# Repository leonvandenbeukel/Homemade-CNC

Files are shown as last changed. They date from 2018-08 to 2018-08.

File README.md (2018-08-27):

## Homemade CNC 

### Warning!

If you want to build one yourself you can download all the necessary files from the V2 directory but I don't have enough time to give you much support so build it at your own risk! :smiley:

### Introduction

This is the second version of my DIY homemade CNC. It's a complete redesign because of some issues that I had with the first one. The main issue with the first version was that the wooden Y axis was getting warped (by moisture I guess). Also the bearings were too small and the aluminium X rails were not strong enough to carry the weight. That's why I've switched over to use 20mm x 20mm square steel tubes for both Y- and X axis. 

### YouTube video

<a href="https://youtu.be/24RslguGy58" target="_blank">Click to view: Homemade CNC with 3D printed parts V2</a>

### Design

I've designed the 3D printed parts with Fusion 360 and used Inkscape for the Y axis drilling template. To control the machine I'm using an Arduino UNO with GRBL firmware and an Arduino CNC Shield. There are plenty of tutorials to find on how to connect and use it so I did not show it in the video. Here are some useful links:

* [GRBL](https://github.com/gnea/grbl)
* [Arduino CNC Shield](https://blog.protoneer.co.nz/arduino-cnc-shield/)

### 3D Printing

The 3D printer I use is an Anet A8. The parts are printed with PLA, mostly 20% infill and 0.2 or 0.4 setting. Use higher infill for parts that must be stronger, for example the stepper motor mounts.

### Cost estimation

* [Link to Google Sheet](https://docs.google.com/spreadsheets/d/e/2PACX-1vQY4hpT6myB3YeNzVlFZfTstJrkYJus8l174NMnyP0J1uP0NMzN-vVNtQ_hvMKP-WXqgEPKxjZSqRSU/pubhtml "Link to Google Sheet")

### Dimensions

Base front multiplex Y panels are 710 x 180 x 22 mm or 28" x 7" x 0.86".
The laminated MDF X Axis side panels are 180 x 370 mm or 7" x 14.4".

The tubes are 20mm x 20mm (0.78") square steel tubes. The length of the Y Axis tubes is 1000mm (40") and the length for the X Axis is approx. 820mm (32"). As an alternative you could also use other dimensions than 20mm x 20mm (maybe even rounded tubes) as long as they are approximately that size.
The Z axis tubes are 15mm x 15mm (0.59") aluminium square tubes, approx. 215mm long (8.5"). You should measure this for yourself, check the video build.

The threaded rods for Y and X rails are 8 mm (0.31") stainless steel.

### Power and motors

To power the NEMA 17 stepper motors I've converted an old ATX PC power supply and used the 12V output. The type of stepper motors I use for the Y- and Z axis are: 17HS19-2004S1, the type for the X axis is: 42BYGHW811. For the wiring I've used CAT5 network cable.

### Software that I mostly use to generate and send GCode:

* bCNC (https://github.com/vlachoudis/bCNC)
* Universal Gcode Sender (https://github.com/winder/Universal-G-Code-Sender)
* Easel by Inventables (http://easel.inventables.com)
* Fusion 360 with CAM (https://www.autodesk.com/products/fusion-360/students-teachers-educators)

### Help me make more stuff!

All my designs are free to use! If you want to support my work you can donate:



Thanks!

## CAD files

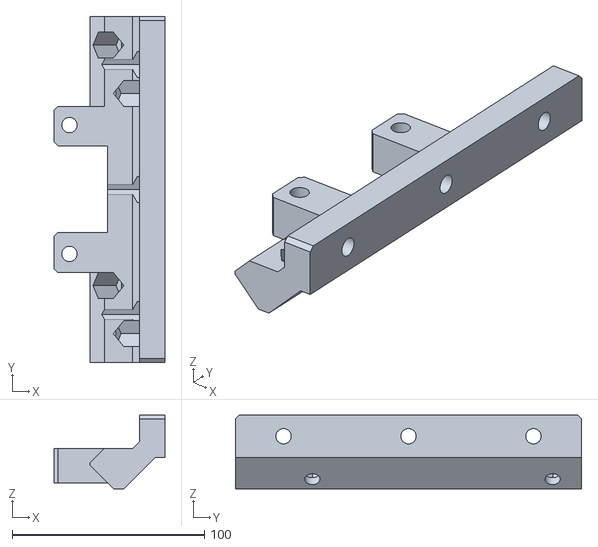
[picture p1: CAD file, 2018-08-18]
V2/Universal Y and X Slider Mount.stl
57.6 x 180.0 x 38.4

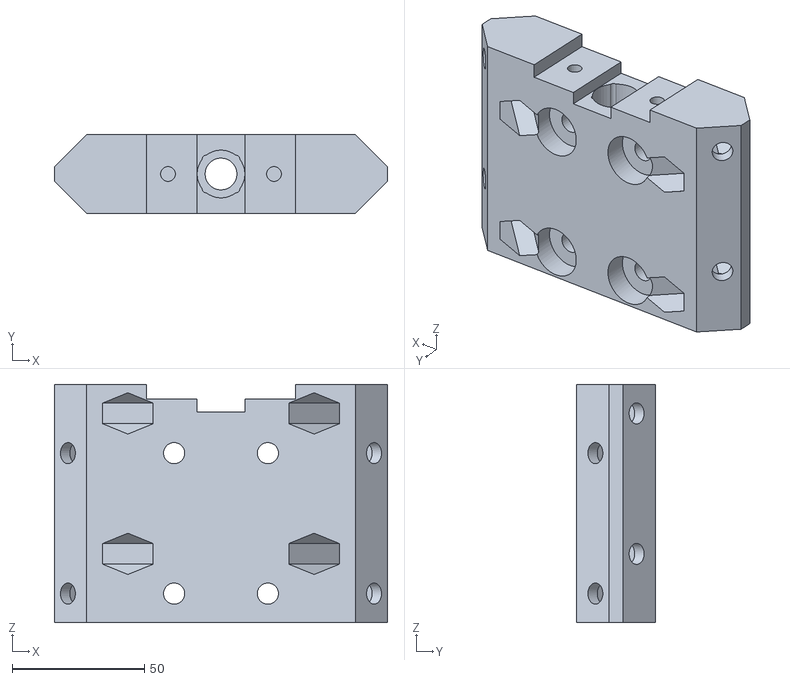
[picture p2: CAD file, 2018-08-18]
V2/Z Axis Mount.stl
125.7 x 29.7 x 90.0

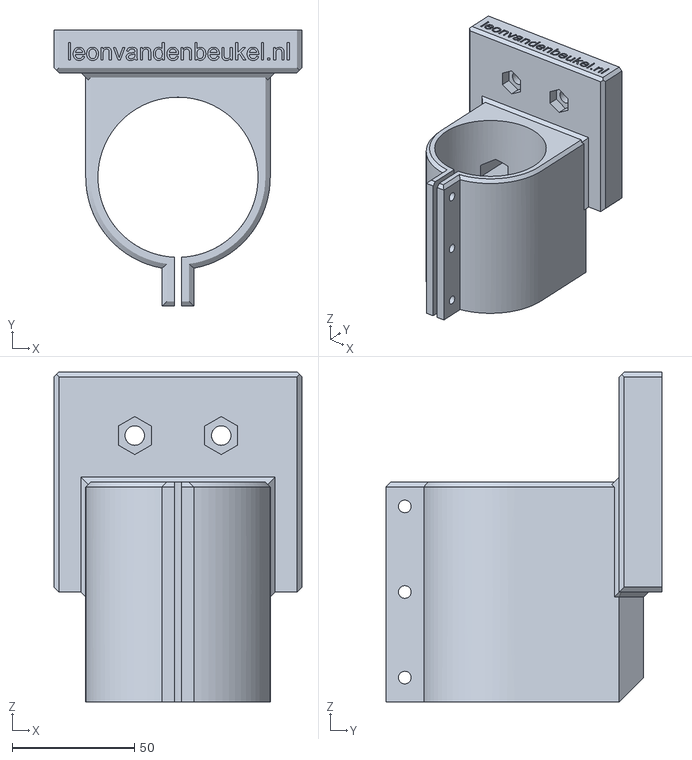
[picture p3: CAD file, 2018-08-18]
V2/Z Axis Router Mount.stl
101.4 x 113.1 x 135.0

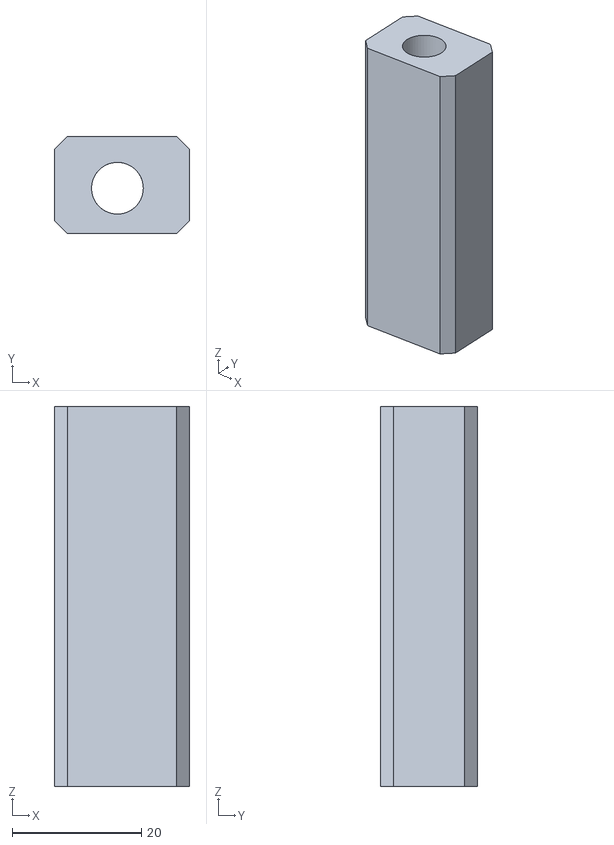
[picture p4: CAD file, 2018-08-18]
V2/X Axis Mount Spacer A.stl
20.9 x 15.0 x 58.7

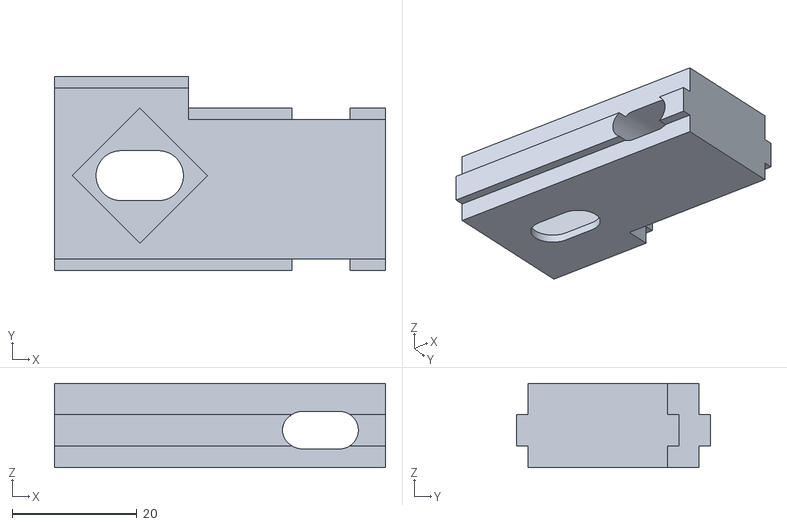
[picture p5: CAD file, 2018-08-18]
V2/Z Axis Slider Bottom.stl
53.0 x 31.0 x 13.5

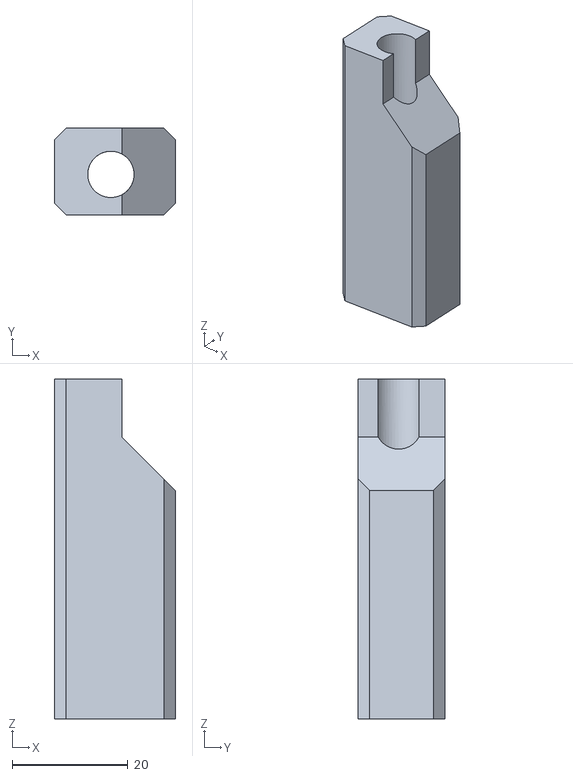
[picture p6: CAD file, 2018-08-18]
V2/X Axis Mount Spacer B.stl
20.9 x 15.0 x 58.7

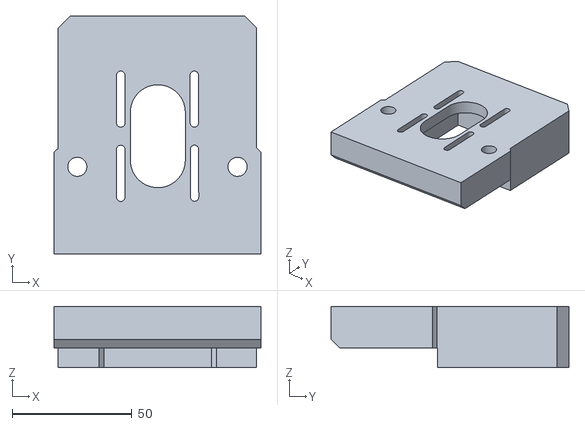
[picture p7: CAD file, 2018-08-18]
V2/Z Axis Stepper Motor Mount.stl
86.6 x 99.4 x 25.6

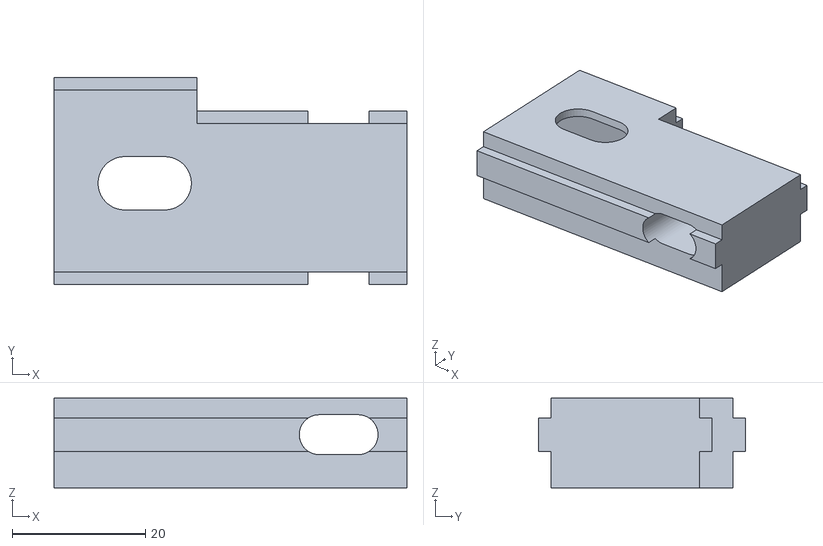
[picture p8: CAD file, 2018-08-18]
V2/Z Axis Slider Top.stl
53.0 x 31.0 x 13.5

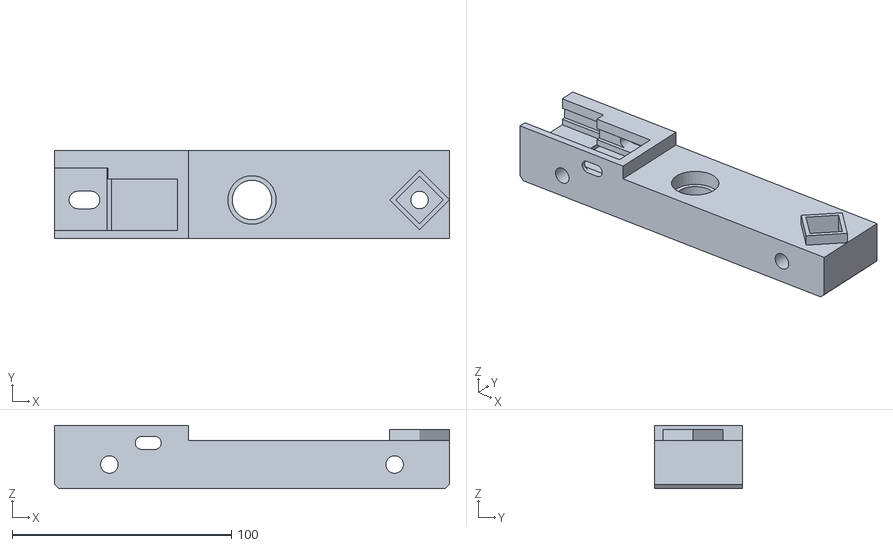
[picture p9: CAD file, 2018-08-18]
V2/Z Axis Bottom.stl
180.0 x 40.0 x 28.9

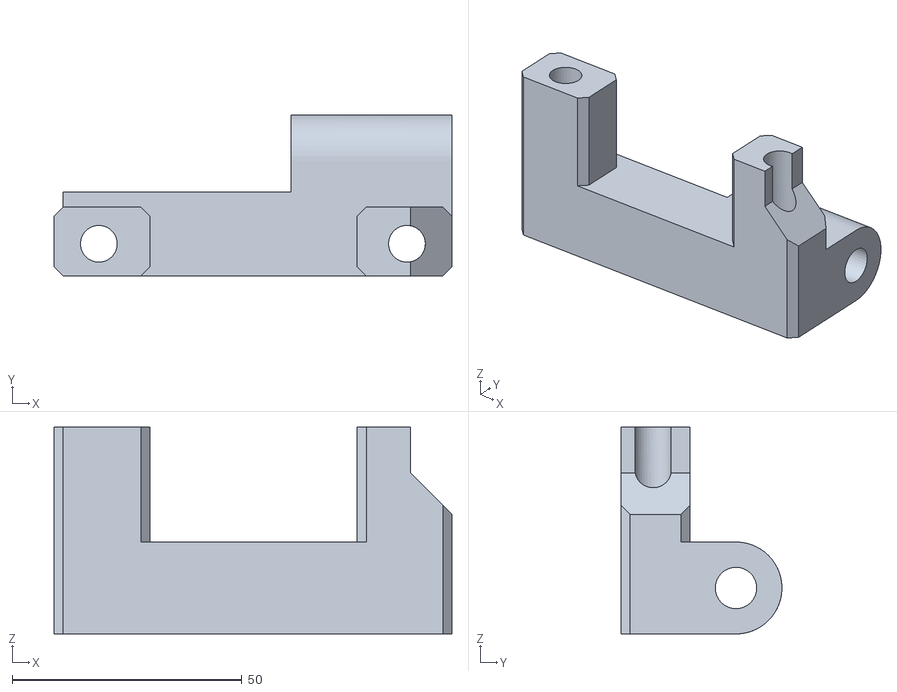
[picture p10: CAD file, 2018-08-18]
V2/X Axis Mount.stl
86.6 x 35.0 x 45.0

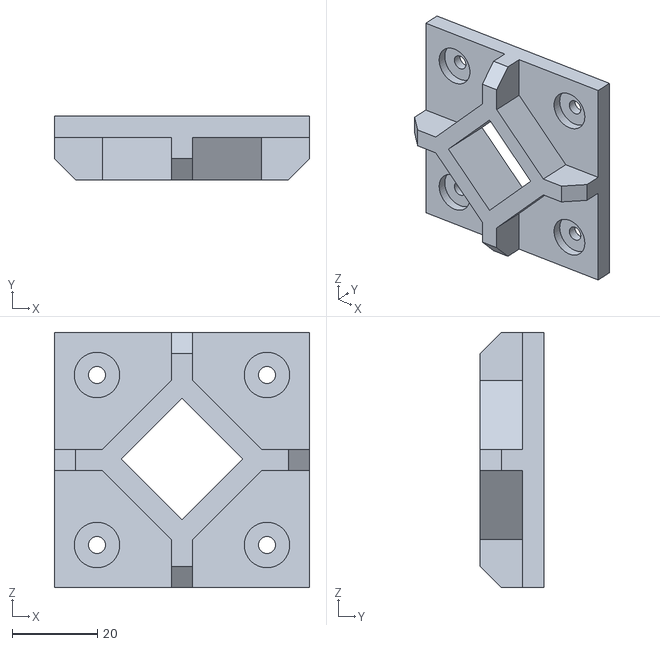
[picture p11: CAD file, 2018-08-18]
V2/Y Axis Rails Mount 20x20.stl
60.0 x 15.0 x 60.0

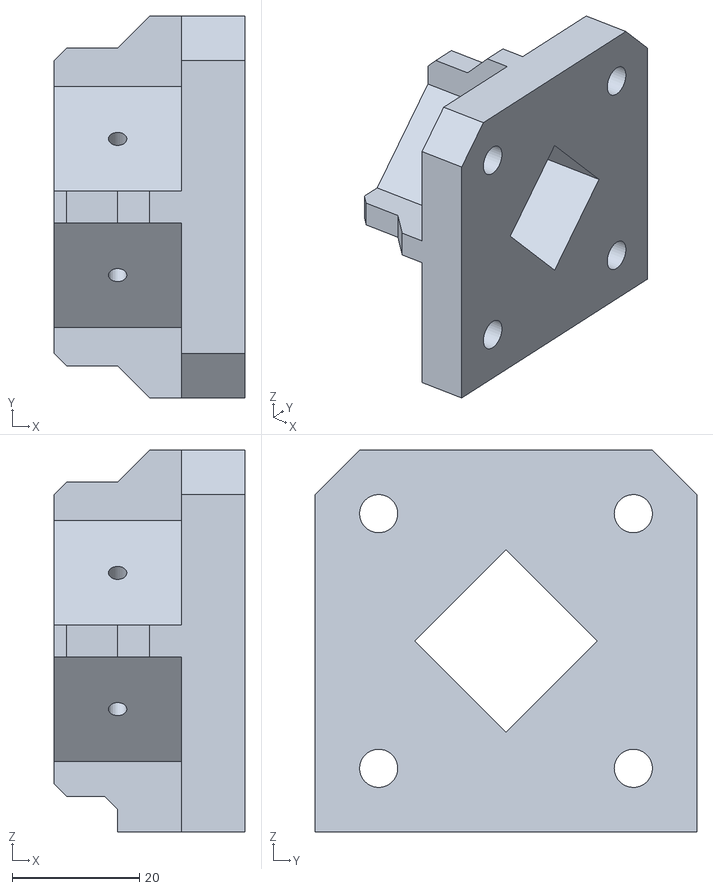
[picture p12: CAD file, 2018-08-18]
V2/X Axis Rails Mount Outside.stl
30.0 x 60.0 x 60.0

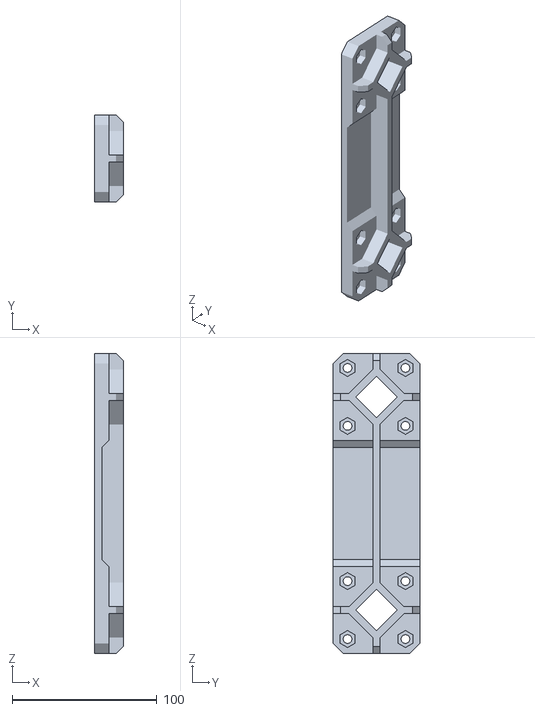
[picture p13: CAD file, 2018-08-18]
V2/X Axis Rails Mount Inside.stl
20.0 x 60.0 x 207.2

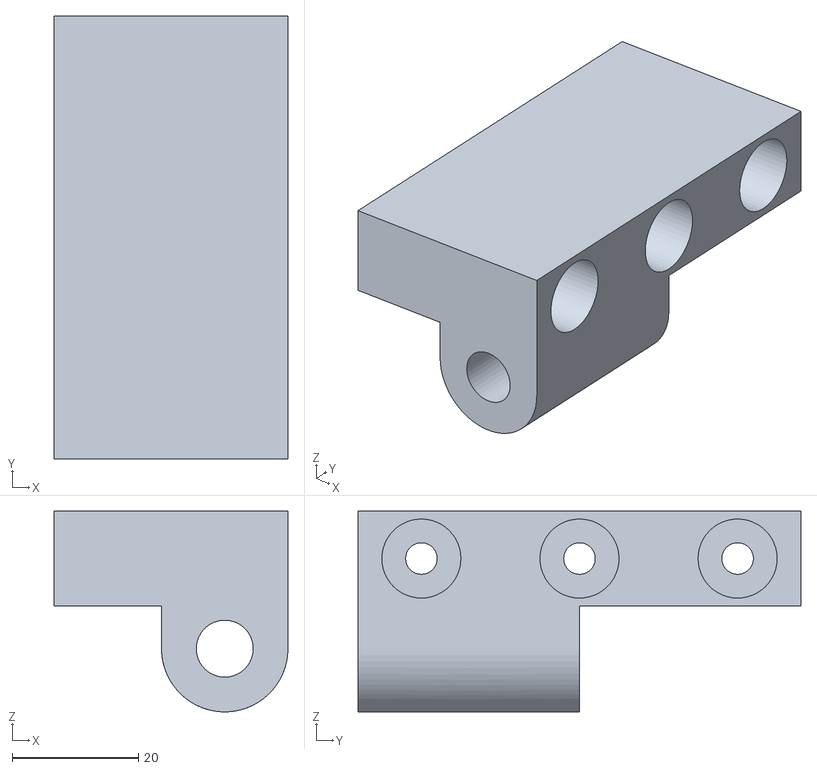
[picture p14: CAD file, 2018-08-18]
V2/Y Axis Threaded Rod Mount.stl
37.0 x 70.0 x 31.7

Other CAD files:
V2/Z Axis Top.stl
V2/Z Axis Mount Backlash.stl
V2/Stepper Motor Mount.stl
V2/Bearing Holder.stl
V1/Router Holder.stl
V1/X Rail holder.stl
V1/Y Carrier Support.stl
V1/Y Carrier.stl
V1/Y Rail Connect Plate.stl
V1/Z Bottom layer.stl
V1/Z First Mounting Plate.stl
V1/Z Forth layer.stl
V1/Z Second Mounting Plate.stl
V1/Z Second layer.stl
V1/Z Third layer.stl
V1/Z Top.stl

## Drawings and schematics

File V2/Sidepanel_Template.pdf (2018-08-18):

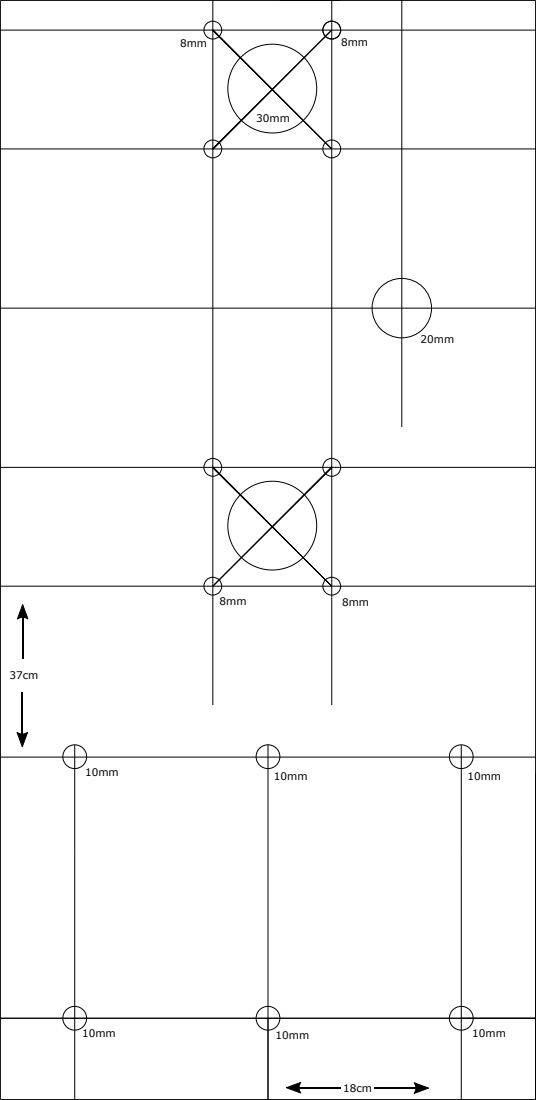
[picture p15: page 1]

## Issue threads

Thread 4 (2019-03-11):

Modifications for DW618

pnbr0014, 2019-03-11:
Hey man this is one amazing build! I would like to build this however, I have a DeWalt DW618 it's a 2 1/4 up router which I think is bigger than yours. If I were to modify the size of the spindle holder to accommodate my router would the rest if the parts be able to handle the extra weight?

pnbr0014, 2019-03-11:
Sorry for some reason it submitted twice

christianlupus, 2019-03-12:
> Sorry for some reason it submitted twice

Then you might close one of the opened issues.

pnbr0014, 2019-03-12:
K I closed it.

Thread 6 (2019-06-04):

Bill of Materials for how many of each STL file?

optimizedsms, 2019-06-04:
Do you happen to have a bill of materials for how many of each STL file needs to be printed?
Thank you.

rjones96, 2019-08-17:
Any update on this? It would be very helpful.

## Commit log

2018-08-17 Moved files
    [Bearing Holder.stl, Router Holder.stl, Stepper Motor Mount.stl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]
2018-08-17 Removed Files
    [Bearing Holder.stl, Router Holder.stl, Stepper Motor Mount.stl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]
2018-08-18 Added the V2 files
    [Bearing Holder.stl, Stepper Motor Mount.stl, Universal Y and X Slider Mount.stl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]
